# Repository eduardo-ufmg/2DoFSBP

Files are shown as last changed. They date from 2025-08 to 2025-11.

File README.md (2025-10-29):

# 2DoFSBP
A two degrees of freedom self balancing pendulum.
3D Drawing: https://cad.onshape.com/documents/dcaab3bd08b5da9e1fdd55d0/

# TODO

## Printing
- [ ] Print a half-wheel pair
- [ ] Conclude motor identification before proceeding
- [ ] Print and test a motor connector
- [ ] Print and test the base
- [ ] Print and test a connector for the wheel guard
- [ ] Print and test a wheel guard
- [ ] Print and test the second set

## Motor Identification
- [ ] Test motor
- [ ] Gather the following information
  - Is the PWM signal active low or active high?
  - Which level in the motor's DIR pin makes it rotate counterclockwise (from the motor's perspective, rather than facing its front)?
  - When the motor is rotating counterclockwise, does the encoder output from [this api](https://github.com/madhephaestus/ESP32Encoder) increment or decrement? (use attachFullQuad and consider 400 pulses per revolution)
- [ ] Create a class for the motor
  - Input signal must be a float in [-1, 1]
  - -1 → max speed clockwise, 1 → max speed counterclockwise
- [ ] Create a class for the encoder
  - Counterclockwise movement increments its position, clockwise decrements it
- [ ] Test both classes
- [ ] Write the code for the identification procedure
  - [ ] Microcontroller
    - Not supposed to compute speed online. Simply collect and transmit the encoder position readings.
    - Use a series of steps large enough for it to approach steady state, but not enough for it to reach it. (See PRBS identification)
    - Collect the input signal to the motor's object and the output signal from the encoder's object at 10 ms
    - Send data to the host at each sampling
    - Avoid blocking operations
  - [ ] Host
    - Listen for the experiment data
    - Store the experiment data when it is finished
    - Preprocess it
      - Remove invalid lines
      - Compute speed and acceleration from the position
    - Fit a standard DC motor transfer function
    - Store it and any available statistic about it
    - Extend it so U(s) is the input signal to the motor's object and Y(s) is the wheel torque
- [ ] Write the code for the model validation procedure
  - [ ] Microcontroller
    - Use the same code that was used for the identification
  - [ ] Host
    - Same acquisition and preprocessing as in the identification procedure
    - Simulate the model for the collected input
    - Compare its output to the captured output from the system

## Pendulum Modeling
- [ ] Capture a simplified geometric model
- [ ] Model the MIMO system with inputs T1 and T2 and outputs Theta and Phi, where:
  - T1 is the torque of the motor that controls Theta
  - T2 is the torque of the motor that controls Phi
  - Theta is the pitch angle
  - Phi is the roll angle
  - Coupling is to be considered

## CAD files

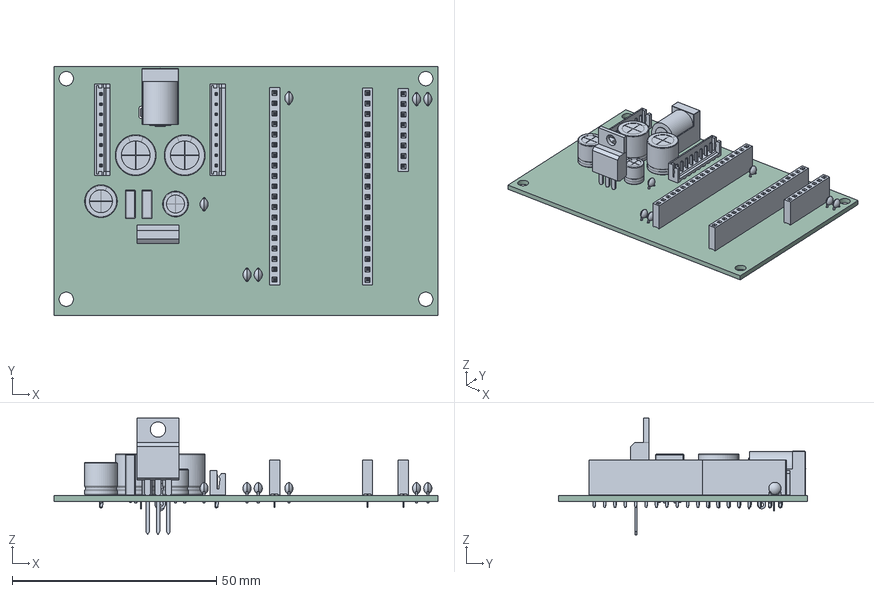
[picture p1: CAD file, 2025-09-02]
CAD/Board/mainboard.step
94.0 x 61.0 x 28.5 mm
CP_Radial_D8.0mm_P3.50mm
C_Disc_D3.0mm_W2.0mm_P2.50mm x 6
PinSocket_1x19_P2.54mm_Vertical x 2
C_Rect_L7.0mm_W2.5mm_P5.00mm x 2
CP_Radial_D6.3mm_P2.50mm
CP_Radial_D10.0mm_P5.00mm x 2
BarrelJack_Horizontal
JST_EH_B8B-EH-A_1x08_P2.50mm_Vertical x 2
TO-220-3_Vertical
PinSocket_1x08_P2.54mm_Vertical
PCB_PCB

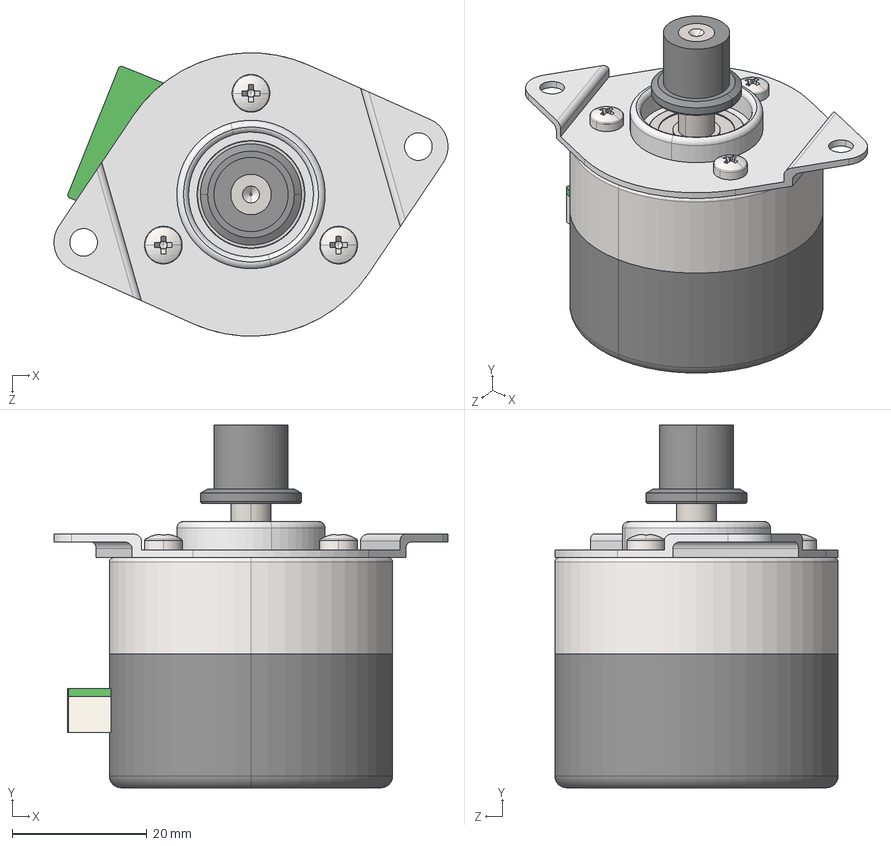
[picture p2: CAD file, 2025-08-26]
CAD/NIDEC24H/Assem1.STEP
58.4 x 53.8 x 42.0 mm
motor
mount_plate
pan head cross recess screw_iso_ISO 7045 - M3 x 4 - Z - 4N x 3
pulley_nidec

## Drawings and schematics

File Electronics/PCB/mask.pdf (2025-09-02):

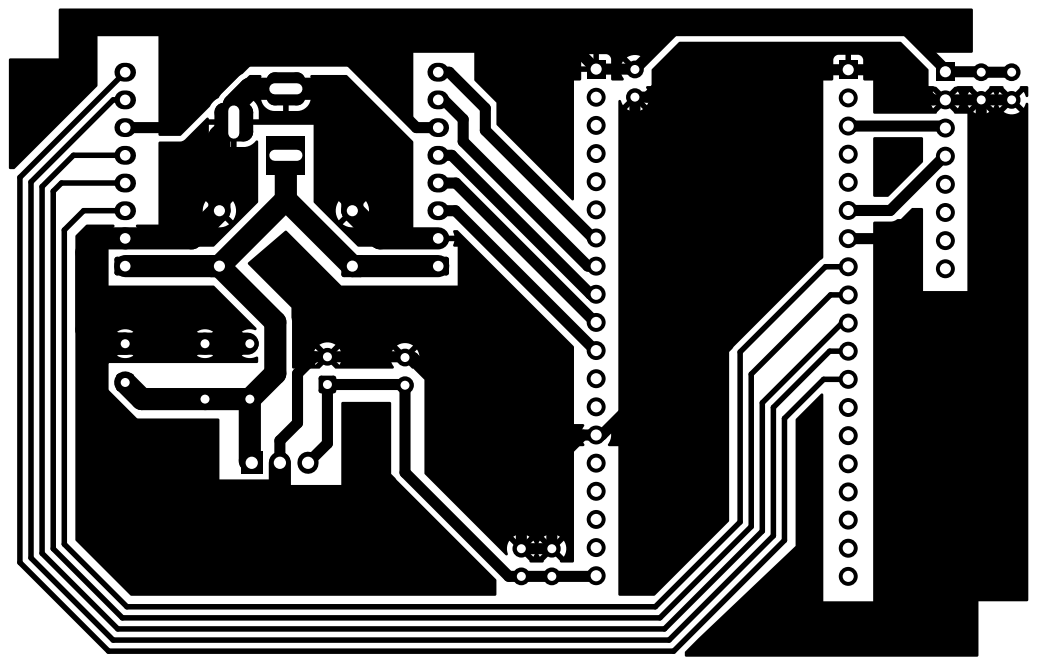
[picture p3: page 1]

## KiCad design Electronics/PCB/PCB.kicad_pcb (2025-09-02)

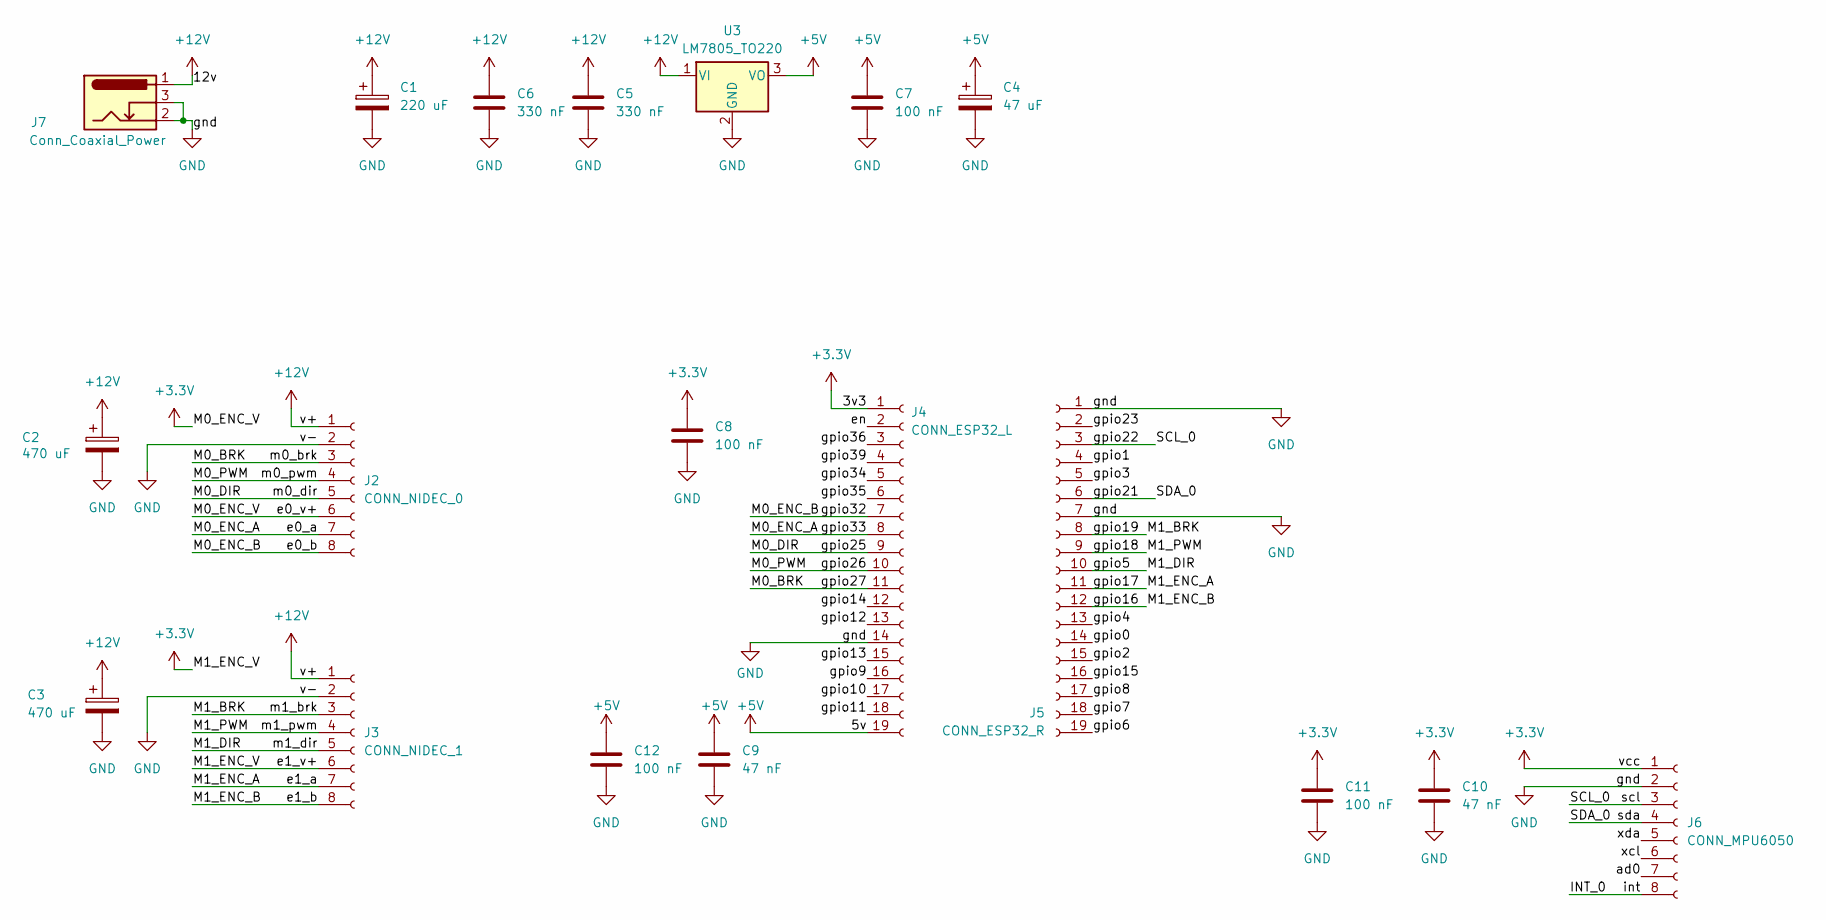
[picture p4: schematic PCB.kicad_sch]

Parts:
C1: 220 uF; CP_Radial_D8.0mm_P3.50mm
C2, C3: 470 uF; CP_Radial_D10.0mm_P5.00mm
C4: 47 uF; CP_Radial_D6.3mm_P2.50mm
C5, C6: 330 nF; C_Rect_L7.0mm_W2.5mm_P5.00mm
C7, C8, C11, C12: 100 nF; C_Disc_D3.0mm_W2.0mm_P2.50mm
C9, C10: 47 nF; C_Disc_D3.0mm_W2.0mm_P2.50mm
J2: CONN_NIDEC_0; JST_EH_B8B-EH-A_1x08_P2.50mm_Vertical
J3: CONN_NIDEC_1; JST_EH_B8B-EH-A_1x08_P2.50mm_Vertical
J4: CONN_ESP32_L; PinSocket_1x19_P2.54mm_Vertical
J5: CONN_ESP32_R; PinSocket_1x19_P2.54mm_Vertical
J6: CONN_MPU6050; PinSocket_1x08_P2.54mm_Vertical
J7: Conn_Coaxial_Power; BarrelJack_Horizontal
U3: LM7805_TO220; TO-220-3_Vertical

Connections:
+3.3V: C8.1, C10.1, C11.1, J2.6, J3.6, J4.1, J6.1
+5V: C4.1, C7.1, C9.1, C12.1, J4.19, U3.3 (VO)
+12V: C1.1, C2.1, C3.1, C5.1, C6.1, J2.1, J3.1, J7.1, U3.1 (VI)
/INT_0: J6.8
/M0_BRK: J2.3, J4.11
/M0_DIR: J2.5, J4.9
/M0_ENC_A: J2.7, J4.8
/M0_ENC_B: J2.8, J4.7
/M0_PWM: J2.4, J4.10
/M1_BRK: J3.3, J5.8
/M1_DIR: J3.5, J5.10
/M1_ENC_A: J3.7, J5.11
/M1_ENC_B: J3.8, J5.12
/M1_PWM: J3.4, J5.9
/SCL_0: J5.3, J6.3
/SDA_0: J5.6, J6.4
/ad0: J6.7
/en: J4.2
/gpio0: J5.14
/gpio1: J5.4
/gpio2: J5.15
/gpio3: J5.5
/gpio4: J5.13
/gpio6: J5.19
/gpio7: J5.18
/gpio8: J5.17
/gpio9: J4.16
/gpio10: J4.17
/gpio11: J4.18
/gpio12: J4.13
/gpio13: J4.15
/gpio14: J4.12
/gpio15: J5.16
/gpio23: J5.2
/gpio34: J4.5
/gpio35: J4.6
/gpio36: J4.3
/gpio39: J4.4
/xcl: J6.6
/xda: J6.5
GND: C1.2, C2.2, C3.2, C4.2, C5.2, C6.2, C7.2, C8.2, C9.2, C10.2, C11.2, C12.2, J2.2, J3.2, J4.14, J5.1, J5.7, J6.2, J7.2, J7.3, U3.2 (GND)

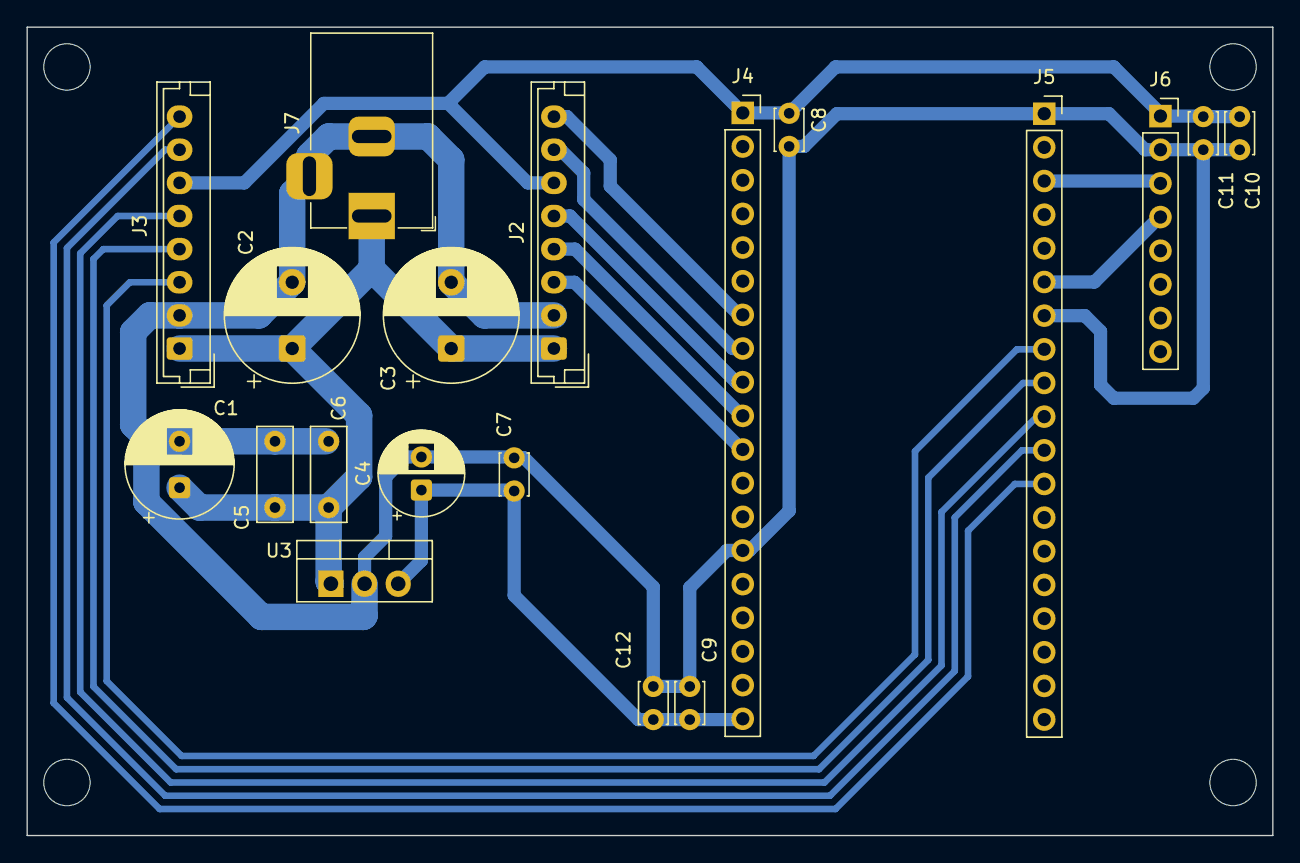
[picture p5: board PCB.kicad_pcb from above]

Board: 2 copper layers, 94.0 x 61.0 mm, 19 parts (0 on the bottom side), 16 nets.

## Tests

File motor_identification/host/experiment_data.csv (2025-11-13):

Time(s) | Input | Angle
0.0 | 0.0 | 12.64491081237793
0.01 | 0.0 | 12.676326751708984
0.02 | 0.0 | 12.739158630371094
0.03 | 0.0 | 12.849114418029785
0.04 | 0.0 | 12.990485191345215
0.05 | 0.0 | 13.178980827331543
0.06 | 0.0 | 13.414600372314453
0.07 | 0.0 | 13.66592788696289
0.08 | 0.0 | 13.980087280273438
0.09 | 0.0 | 14.309954643249512
0.1 | 0.0 | 14.702653884887695
0.11 | 0.0 | 15.126769065856934
0.12 | 0.0 | 15.58229923248291
0.13 | 0.0 | 16.069246292114258
0.14 | 0.0 | 16.6190242767334
0.15 | 0.0 | 17.184511184692383
0.16 | 0.0 | 17.797122955322266
0.17 | 0.0 | 18.44114875793457
0.18 | 0.0 | 19.132299423217773
0.19 | 0.0 | 19.839157104492188
0.2 | 0.0 | 20.608848571777344
0.21 | -0.06718355417251587 | 21.362829208374023
0.22 | -0.06718355417251587 | 22.116811752319336
0.23 | -0.06718355417251587 | 22.855087280273438
0.24 | -0.06718355417251587 | 23.593360900878906
0.25 | -0.06718355417251587 | 24.30021858215332
0.26 | -0.06718355417251587 | 25.007078170776367
0.27 | -0.06718355417251587 | 25.69822883605957
0.28 | -0.06718355417251587 | 26.37367057800293
0.29 | -0.06718355417251587 | 27.033405303955078
0.3 | -0.06718355417251587 | 27.677431106567383
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

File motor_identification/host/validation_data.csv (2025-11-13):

Time(s) | Input | Real_Angle | Velocity | Acceleration | Real_Torque
0.0 | 0.0 | -0.0 | 0.8311696032173828 | 391.7835405343885 | 0.10754458187668965
0.01 | 0.0 | 0.03141592815518379 | 4.749005201772712 | 391.7835791766773 | 0.10754459248399792
0.02 | 0.0 | 0.09424778074026108 | 8.66684118675093 | 391.7836178189661 | 0.10754460309130619
0.03 | 0.0 | 0.2042035162448883 | 12.584677558152036 | 391.78365646125485 | 0.10754461369861446
0.04 | 0.0 | 0.3455751836299896 | 16.502514315976025 | 391.78369510354366 | 0.10754462430592274
0.05 | 0.0 | 0.5340707302093506 | 20.42035146022291 | 391.7837337458319 | 0.10754463491323087
0.06 | 0.0 | 0.7539822459220886 | 24.347343081036733 | 393.61449935427805 | 0.10804718007274933
0.07 | 0.0 | 1.0210176706314087 | 28.274334967715276 | 391.783707521177 | 0.10754462771456309
0.08 | 0.0 | 1.3194688558578491 | 32.20132614812279 | 393.6144390028377 | 0.10804716350627895
0.09 | 0.0 | 1.6650440692901611 | 36.12831653137027 | 391.7836496879981 | 0.10754461183935547
0.1 | 0.0 | 2.0420353412628174 | 40.14684454637064 | 388.1221106558104 | 0.10653951937501996
0.11 | 0.0 | 2.4661502838134766 | 43.98412553950992 | 384.0945303301123 | 0.10543394857561583
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

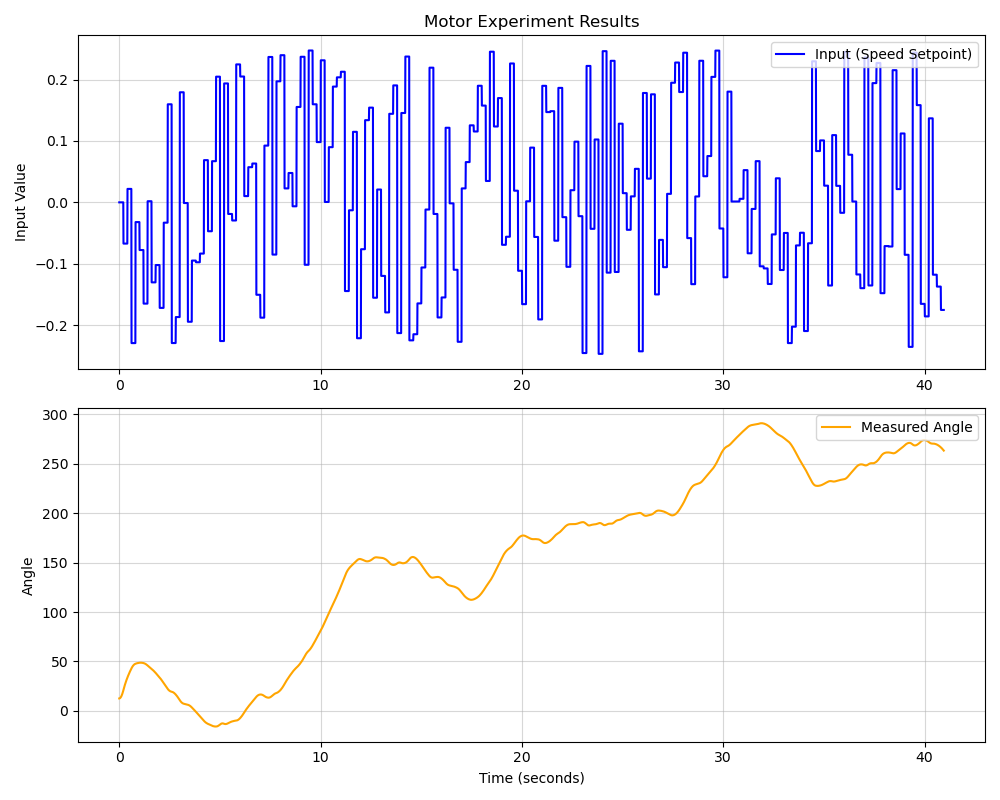
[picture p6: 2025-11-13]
motor_identification/host/experiment_results.png

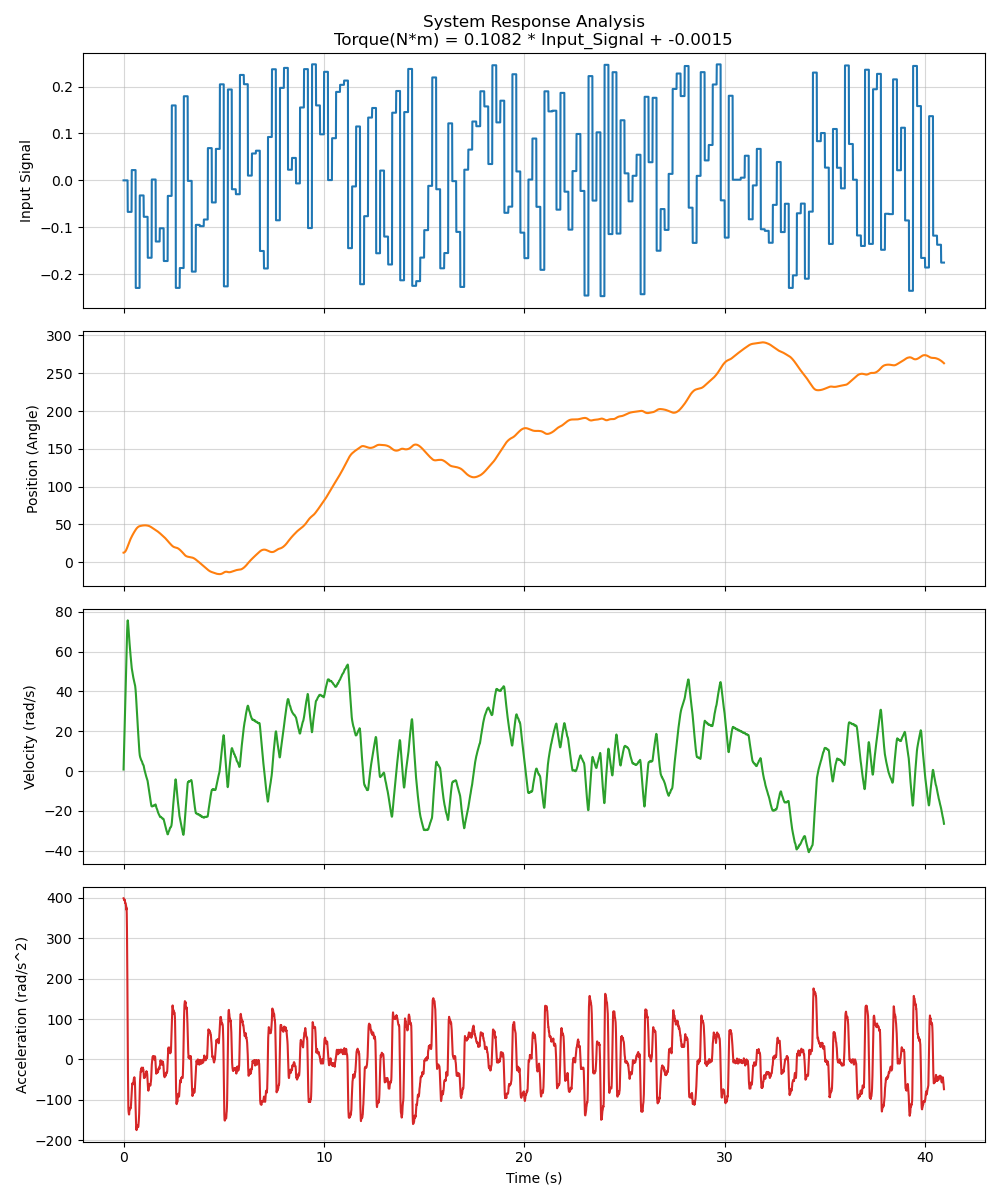
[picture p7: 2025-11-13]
motor_identification/host/estimation_results.png

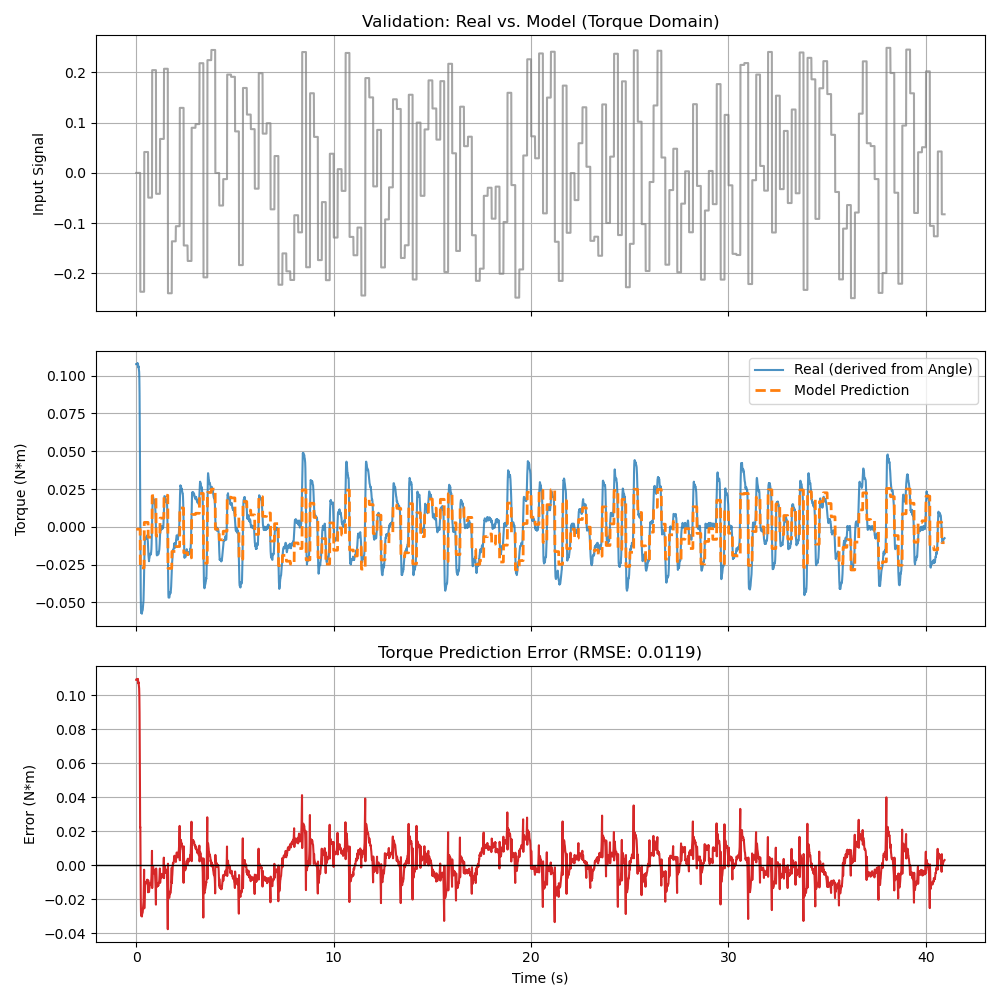
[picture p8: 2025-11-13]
motor_identification/host/validation_results.png

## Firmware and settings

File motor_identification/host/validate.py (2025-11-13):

import serial
import time
import struct
import csv
import json
import pandas as pd
import numpy as np
import matplotlib.pyplot as plt
import os
import sys
from scipy.signal import savgol_filter

# --- Configuration ---
SERIAL_PORT = '/dev/ttyUSB0' 
BAUD_RATE = 115200
TEST_DATA_LENGTH = 4096
TIMEOUT_SEC = 2
SAMPLE_PERIOD_SEC = 0.01
MODEL_FILE = 'model_parameters.json'

# --- Protocol Definitions ---
HOST_CHECK_CONNECTION   = b'\x01'
DEVICE_CHECK_CONNECTION = b'\x02'
HOST_START_TEST         = b'\x03'
DEVICE_ACK_START        = b'\x04'
DEVICE_TEST_SUCCESS     = b'\x05'
HOST_REQUEST_DATA       = b'\x06'
DEVICE_DATA_REQUEST_ACK = b'\x07'
DEVICE_DATA_STREAM_START = b'DATA_START'
DEVICE_DATA_STREAM_END   = b'DATA_END'

def run_experiment_and_process_data(inertia_value):
    """
    Runs experiment, downloads data, and computes derivatives 
    to recover Real Torque.
    """
    print("\n--- 1. Hardware Interface ---")
    try:
        ser = serial.Serial(SERIAL_PORT, BAUD_RATE, timeout=TIMEOUT_SEC)
        time.sleep(2) 
    except serial.SerialException as e:
        print(f"Error opening serial port {SERIAL_PORT}: {e}")
        return None

    try:
        ser.reset_input_buffer()
        ser.reset_output_buffer()

        # 1. Check connection
        print("Connecting to controller...")
        ser.write(HOST_CHECK_CONNECTION)
        while ser.read(1) != DEVICE_CHECK_CONNECTION:
            pass
        print("   -> Connection confirmed.")

        # 2. User Start
        input("Press [Enter] to start the validation experiment...")

        # 3. Start Test
        print("Sending start command...")
        ser.write(HOST_START_TEST)

        if ser.read(1) != DEVICE_ACK_START:
            print("Error: Device did not acknowledge start.")
            return None
        print("   -> Test running...")

        # 4. Wait for completion
        print("Waiting for test completion (~41 seconds)...")
        ser.timeout = 60 
        if ser.read(1) != DEVICE_TEST_SUCCESS:
            print("Error: Test failed or timed out.")
            return None
        print("   -> Test completed.")
        ser.timeout = TIMEOUT_SEC 

        # 5. Request Data
        print("Requesting data...")
        ser.write(HOST_REQUEST_DATA)

        if ser.read(1) != DEVICE_DATA_REQUEST_ACK:
            print("Error: Device did not ack data request.")
            return None

        # 6. Read Data
        print("Downloading data stream...")
        if ser.read(len(DEVICE_DATA_STREAM_START)) != DEVICE_DATA_STREAM_START:
            print("Error: Invalid header.")
            return None

        bytes_to_read = TEST_DATA_LENGTH * 4
        raw_input = ser.read(bytes_to_read)
        raw_angle = ser.read(bytes_to_read)

        if ser.read(len(DEVICE_DATA_STREAM_END)) != DEVICE_DATA_STREAM_END:
            print("Warning: Invalid footer.")

        fmt = f'<{TEST_DATA_LENGTH}f'
        input_values = struct.unpack(fmt, raw_input)
        angle_values = struct.unpack(fmt, raw_angle)
        
        # Create DataFrame
        time_axis = [i * SAMPLE_PERIOD_SEC for i in range(TEST_DATA_LENGTH)]
        df = pd.DataFrame({
            'Time(s)': time_axis,
            'Input': input_values,
            'Real_Angle': angle_values
        })
        
        # --- Process Derivatives to find Real Torque ---
        print("Computing Real Torque from Angle data...")
        dt = SAMPLE_PERIOD_SEC
        window_length = 11 
        poly_order = 3

        # 1. Velocity
        df['Velocity'] = savgol_filter(df['Real_Angle'], window_length, poly_order, deriv=1, delta=dt)
        # 2. Acceleration
        df['Acceleration'] = savgol_filter(df['Real_Angle'], window_length, poly_order, deriv=2, delta=dt)
        # 3. Real Torque (Tau = I * alpha)
        df['Real_Torque'] = inertia_value * df['Acceleration']

        filename = 'validation_data.csv'
        df.to_csv(filename, index=False)
        print(f"   -> Data saved to {filename}")
        
        return df

    except Exception as e:
        print(f"Error during experiment: {e}")
        return None
    finally:
        if ser.is_open:
            ser.close()

def load_model_parameters():
    """Loads parameters from JSON. Raises error if not found."""
    if not os.path.exists(MODEL_FILE):
        print(f"\n[ERROR] Model file '{MODEL_FILE}' not found.")
        print("Please run 'estimate.py' first to generate the model parameters.")
        sys.exit(1)

    try:
        with open(MODEL_FILE, 'r') as f:
            data = json.load(f)
            print(f"\n[INFO] Automatically loaded model from '{MODEL_FILE}'")
            return data['slope'], data['intercept'], data['inertia']
    except Exception as e:
        print(f"\n[ERROR] Failed to read '{MODEL_FILE}': {e}")
        sys.exit(1)

def main():
    print("=== System Validation Tool (Torque Domain) ===")
    
    # 1. Load Model First (Need Inertia for data processing)
    slope, intercept, inertia = load_model_parameters()
    print(f"Model: Torque = {slope:.4f} * Input + {intercept:.4f}")
    print(f"Inertia: {inertia:.6e}")

    # 2. Run Experiment & Calculate Real Torque
    df = run_experiment_and_process_data(inertia)
    if df is None:
        return

    # 3. Calculate Predicted Torque
    print("\n--- 2. Model Prediction ---")
    # Model: Torque = K * Input + Offset
    df['Predicted_Torque'] = (slope * df['Input']) + intercept

    # 4. Analysis
    # RMSE on Torque
    rmse = np.sqrt(((df['Real_Torque'] - df['Predicted_Torque']) ** 2).mean())
    
    print("\n--- Validation Results ---")
    print(f"Torque RMSE: {rmse:.4f} N*m")

    # 5. Plotting
    print("Plotting comparison...")
    fig, axs = plt.subplots(3, 1, figsize=(10, 10), sharex=True)

    # Plot 1: Input
    axs[0].plot(df['Time(s)'], df['Input'], color='gray', alpha=0.7)
    axs[0].set_ylabel('Input Signal')
    axs[0].set_title('Validation: Real vs. Model (Torque Domain)')
    axs[0].grid(True)

    # Plot 2: Torque Comparison
    axs[1].plot(df['Time(s)'], df['Real_Torque'], label='Real (derived from Angle)', color='tab:blue', linewidth=1.5, alpha=0.8)
    axs[1].plot(df['Time(s)'], df['Predicted_Torque'], label='Model Prediction', color='tab:orange', linestyle='--', linewidth=2)
    axs[1].set_ylabel('Torque (N*m)')
    axs[1].legend(loc='upper right')
    axs[1].grid(True)

    # Plot 3: Error Residuals
    error = df['Real_Torque'] - df['Predicted_Torque']
    axs[2].plot(df['Time(s)'], error, color='tab:red')
    axs[2].set_ylabel('Error (N*m)')
    axs[2].set_xlabel('Time (s)')
    axs[2].axhline(0, color='black', linewidth=1)
    axs[2].grid(True)
    axs[2].set_title(f'Torque Prediction Error (RMSE: {rmse:.4f})')

    plt.tight_layout()
    plt.savefig('validation_results.png')
    print("Results saved to validation_results.png. Displaying...")
    plt.show()

if __name__ == "__main__":
    main()

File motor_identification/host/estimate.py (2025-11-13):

import pandas as pd
import numpy as np
import matplotlib.pyplot as plt
from scipy.signal import savgol_filter
from scipy import stats
import json

# --- Configuration ---
INPUT_FILENAME = 'experiment_data.csv'
OUTPUT_MODEL_FILE = 'model_parameters.json'

# --- Hardcoded Physics Constants ---
# Shape: Ring (Thick-walled cylinder)
MASS = 0.09          # kg
RADIUS_INNER = 0.05  # meters
RADIUS_OUTER = 0.06  # meters

def main():
    print("--- Motor Parameter Estimator ---")

    # 1. Read experiment data
    try:
        print(f"Reading data from {INPUT_FILENAME}...")
        df = pd.read_csv(INPUT_FILENAME)
    except FileNotFoundError:
        print(f"Error: Could not find {INPUT_FILENAME}. Run experiment.py first.")
        return

    # Check columns
    required_cols = ['Time(s)', 'Input', 'Angle']
    if not all(col in df.columns for col in required_cols):
        print(f"Error: CSV missing columns. Found: {df.columns}. Expected: {required_cols}")
        return

    # 2. Clean data & Compute Derivatives
    print("Processing data...")
    dt = df['Time(s)'].diff().mean()
    
    # Savitzky-Golay filter settings
    window_length = 11 
    poly_order = 3

    df['Velocity'] = savgol_filter(df['Angle'], window_length, poly_order, deriv=1, delta=dt)
    df['Acceleration'] = savgol_filter(df['Angle'], window_length, poly_order, deriv=2, delta=dt)

    # 3. Physics Calculation
    print(f"Load Properties: Ring (Mass={MASS}kg, R_in={RADIUS_INNER}m, R_out={RADIUS_OUTER}m)")
    
    # Inertia for thick-walled ring
    inertia = 0.5 * MASS * (RADIUS_INNER**2 + RADIUS_OUTER**2)
    print(f"Calculated Moment of Inertia (I): {inertia:.6e} kg*m^2")

    df['Estimated_Torque'] = inertia * df['Acceleration']

    # 4. Estimate Transfer Function
    slope, intercept, r_value, p_value, std_err = stats.linregress(df['Input'], df['Estimated_Torque'])
    
    transfer_function_str = f"Torque(N*m) = {slope:.4f} * Input_Signal + {intercept:.4f}"
    
    print("\n--- Results ---")
    print(f"Transfer Function: {transfer_function_str}")
    print(f"Correlation (R^2): {r_value**2:.4f}") # type: ignore

    # 5. Save Model to JSON
    model_data = {
        "slope": slope,
        "intercept": intercept,
        "inertia": inertia,
        "mass": MASS,
        "note": "Generated by estimate.py"
    }
    
    try:
        with open(OUTPUT_MODEL_FILE, 'w') as f:
            json.dump(model_data, f, indent=4)
        print(f"\n[SUCCESS] Model parameters saved to '{OUTPUT_MODEL_FILE}'.")
        print("You can now run validate.py without manual input.")
    except Exception as e:
        print(f"Error saving model file: {e}")

    # 6. Plotting
    print("Plotting results...")
    fig, axs = plt.subplots(4, 1, figsize=(10, 12), sharex=True)
    
    axs[0].plot(df['Time(s)'], df['Input'], color='tab:blue')
    axs[0].set_ylabel('Input Signal')
    axs[0].set_title(f'System Response Analysis\n{transfer_function_str}')
    axs[0].grid(True, alpha=0.5)

    axs[1].plot(df['Time(s)'], df['Angle'], color='tab:orange')
    axs[1].set_ylabel('Position (Angle)')
    axs[1].grid(True, alpha=0.5)

    axs[2].plot(df['Time(s)'], df['Velocity'], color='tab:green')
    axs[2].set_ylabel('Velocity (rad/s)')
    axs[2].grid(True, alpha=0.5)

    axs[3].plot(df['Time(s)'], df['Acceleration'], color='tab:red')
    axs[3].set_ylabel('Acceleration (rad/s^2)')
    axs[3].set_xlabel('Time (s)')
    axs[3].grid(True, alpha=0.5)
    
    plt.tight_layout()
    plt.savefig('estimation_results.png')
    print("Plot saved to 'estimation_results.png'. Displaying...")
    plt.show()

if __name__ == "__main__":
    main()

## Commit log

2025-08-26 name esp conn pins
    [Assem1.STEP, mainboard.kicad_pcb, mainboard.kicad_sch]
2025-08-26 assign footprints
    [mainboard.kicad_sch]
2025-08-27 export mainboard step
    [mainboard.kicad_pcb, mainboard.kicad_sch]
2025-08-28 improve PCB
    [mainboard.kicad_pcb]
2025-08-30 drawn pcb
    [PCB.kicad_pcb, PCB.kicad_sch, perfboard.kicad_pcb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]
2025-09-02 fix pcb
    [PCB.kicad_pcb, mainboard.step]
2025-09-02 fix hole placement
    [PCB.kicad_pcb, mainboard.step]
2025-09-24 Update visible layers in PCB files and set BOM export filename path
2025-10-29 Add initial implementations for experiment, estimation, and validation modules
    - Created estimate.py to handle data reading, cleaning, and computation of velocity and acceleration, along with torque estimation.
    - Developed experiment.py for managing the experiment lifecycle, including connection checks, data acquisition, and success reporting.
    - Implemented validate.py to facilitate validation processes, including input signal capture, model comparison, and result reporting.
2025-11-13 Implement communication functions for motor control and data handling
2025-11-13 Implement the experiment script
    [experiment_data.csv]
2025-11-13 Improve logging and plot data
    [experiment_data.csv]
2025-11-13 Save time instead of index
    [experiment_data.csv]
2025-11-13 Estimate and validade
    [experiment_data.csv, validation_data.csv]
